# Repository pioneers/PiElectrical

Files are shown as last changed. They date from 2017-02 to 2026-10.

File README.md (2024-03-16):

# PiElectrical

This is the working repo for PiElectrical teams

1. [ToDo](#todo)
2. [Repo Structure](#repo-structure)
3. [Setup](#setup)
4. [Work Flow](#work-flow)
5. [How to Create a Gerber](#how-to-create-a-gerber)
6. [Docu Packets](#docu-packets)
7. [FAQ](#faq)
8. [Useful Links](#useful-links)
9. [Standards](#standards)

## ToDo:
* The stuff in PDB-Y16
* Convert motor controller design to KiCad
* Add and test current regulation for motor controller
* Talk to runtime and potentially use cheaper MCU for motor controller

[Back to Top](#pielectrical)

## Repo Structure:

**Boards**: Contains all necessary information about each board, including KiCad (and old Eagle) files, arduino test files, and board specific documentation.

**Bootloaders**: Contains the files necessary to burn the bootloader for boards identifying as Leonardo (Atmega32u4).

**Documentation**: All docu packets and scripts. *Fragile! Do not touch!*

**Production_Files**: Finalized gerbs and other necessary production files (BOM, CPL, etc...) sent out for fabrication.

**Images**: Place all your images in here to enhance your READMEs.

**Libraries**: Necessary KiCad files to work on PiElectrical

ToDo is on the README to keep things easier to see at first glance. GitHub issues tracker can be used as well.

[Back to Top](#pielectrical)

## Setup

<details>
    <summary>When you see an arrow like this... (click me)</summary>
        ...it indicates an expandable section. We usually include images in here as a better reference for you to follow along.
</details>

### Initial Setup of PiElectrical repo on your computer

1. Copy the URL for pioneers/PiElectrical to your clipboard: (Or here: https://github.com/pioneers/PiElectrical.git)
2. In Terminal (Mac, GNU/Linux) or Git Bash (windows), navigate to your working directory (the directory that you want to keep PiElectrical in.)
3. Clone PiElectrical by running this command: `git clone https://github.com/pioneers/PiElectrical.git`

### Installation of KiCad on your computer
1. Download the latest version of KiCad here: https://www.kicad.org/download/
2. <details>
    <summary>Run installer. Use all default settings on installer. (Click to see default settings)<br></summary>
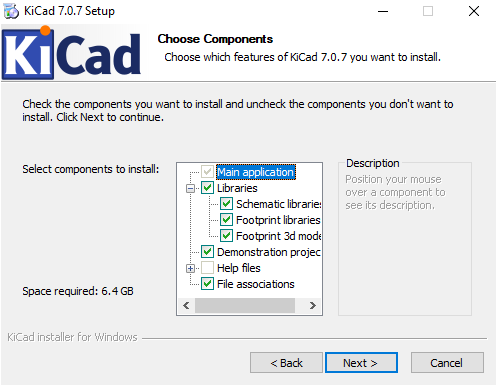
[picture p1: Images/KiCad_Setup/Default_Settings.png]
    
</details>

### Setting up KiCad
1. Open KiCad.
2. <details>
    <summary>Depending on whether you've used KiCad before, select the appropriate option on the pop-up. (Default settings if you're new to KiCad).</summary>
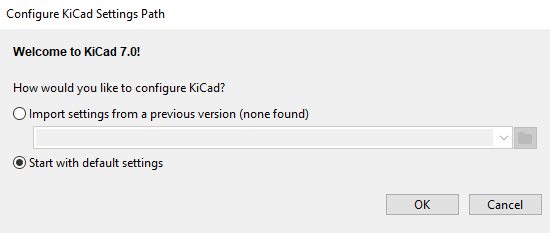
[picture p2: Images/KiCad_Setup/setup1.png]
    
   </details>

#### Adding Symbols
1. <details>
    <summary>Go to the <i>Preferences</i> tab, and select <i>Manage Symbol Libraries...</i></summary>
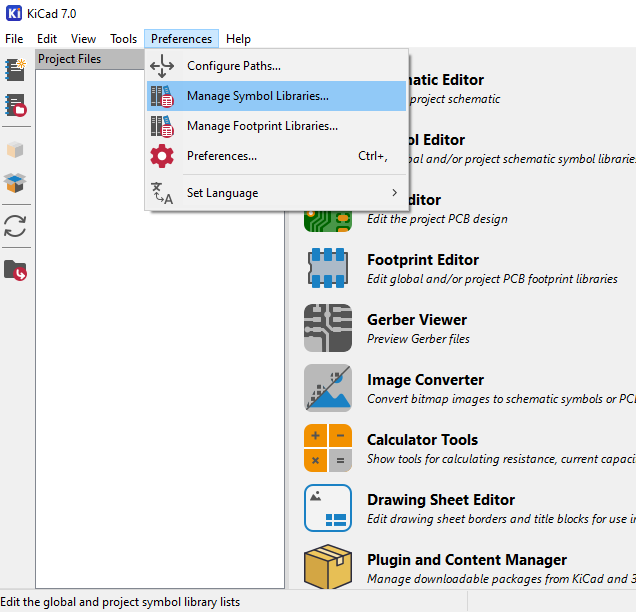
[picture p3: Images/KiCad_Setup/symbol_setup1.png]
    
   </details>
2. <details>
    <summary>If this is your first time using KiCad, it will prompt you to configure the <i>Global Symbol Library</i>. It is highly recommended that you select "Copy default global symbol library table".</summary>
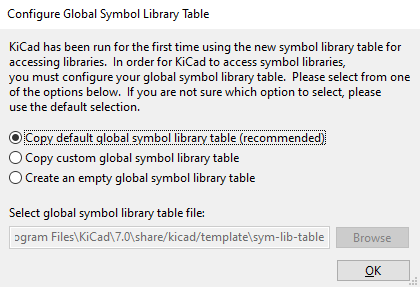
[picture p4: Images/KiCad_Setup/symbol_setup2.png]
    
   </details>
3. <details>
    <summary>Select the folder icon near the bottom left and navigate to the <i>PiE_Symbols.kicad_sym</i> file in the <i>src</i> folder.</summary>
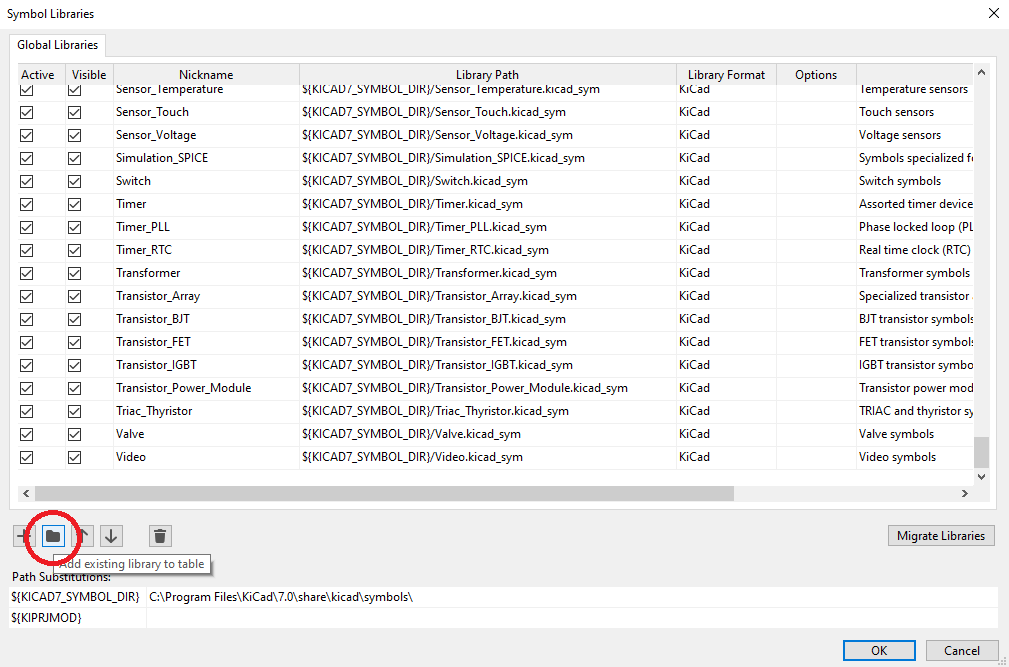
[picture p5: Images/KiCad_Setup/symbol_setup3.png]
    
   </details>
4. <details>
    <summary>You should now see the <i>PiE_Symbols</i> in your Symbol Libraries. Make sure the "active" box is checked, and click "OK".</summary>
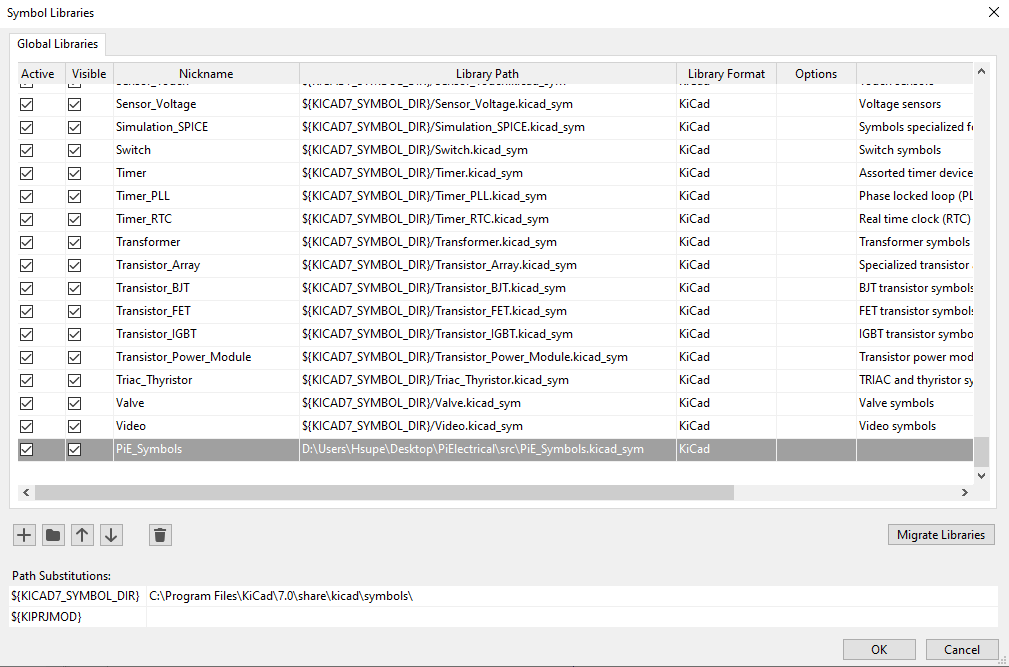
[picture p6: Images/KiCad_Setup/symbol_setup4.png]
    
   </details>

#### Adding Footprints
1. <details>
    <summary>Go to the <i>Preferences</i> tab, and select <i>Manage Footprint Libraries...</i></summary>
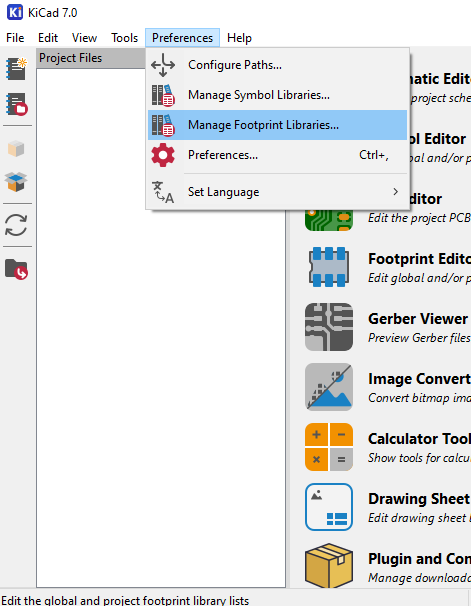
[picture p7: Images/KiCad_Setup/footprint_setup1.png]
    
   </details>
2. <details>
    <summary>If this is your first time using KiCad, it will prompt you to configure the <i>Global Footprint Library</i>. It is highly recommended that you select "Copy default global footprint library table".</summary>
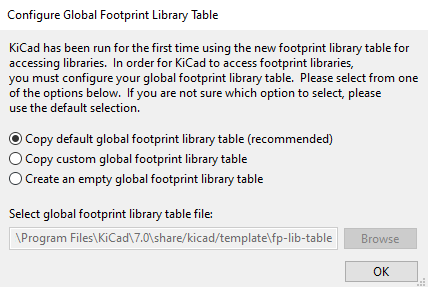
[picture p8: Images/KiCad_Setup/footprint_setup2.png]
    
   </details>
3. <details>
    <summary>Select the folder icon near the bottom left and navigate to the <i>PiE_Footprints.pretty</i> file in the <i>src</i> folder.</summary>
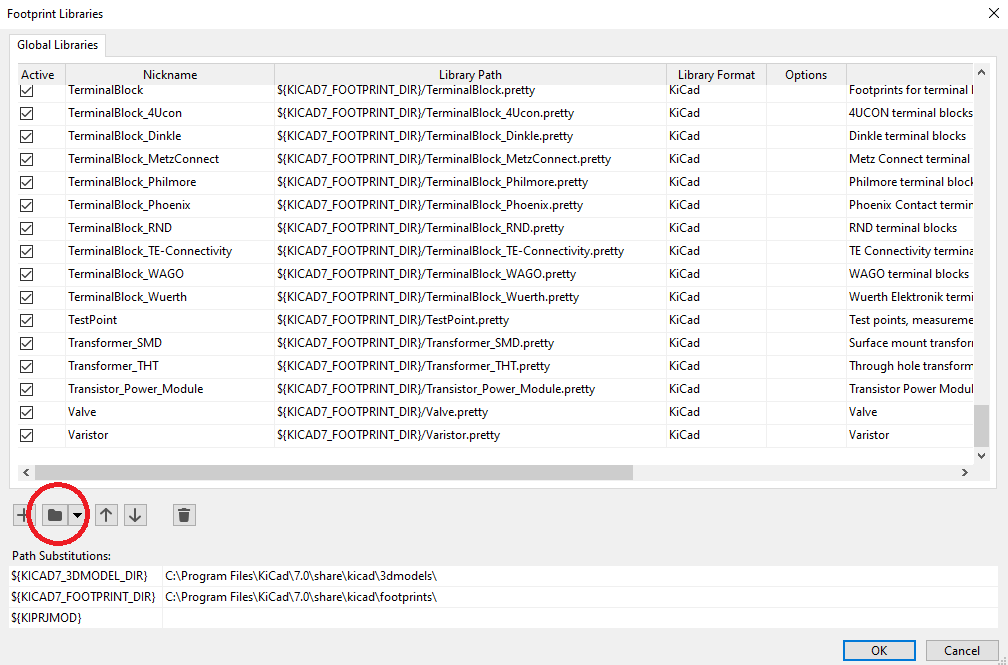
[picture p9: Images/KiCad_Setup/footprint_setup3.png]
    
   </details>
4. <details>
    <summary>You should now see the <i>PiE_Footprints</i> in your Footprint Libraries. Make sure the "active" box is checked, and click "OK".</summary>
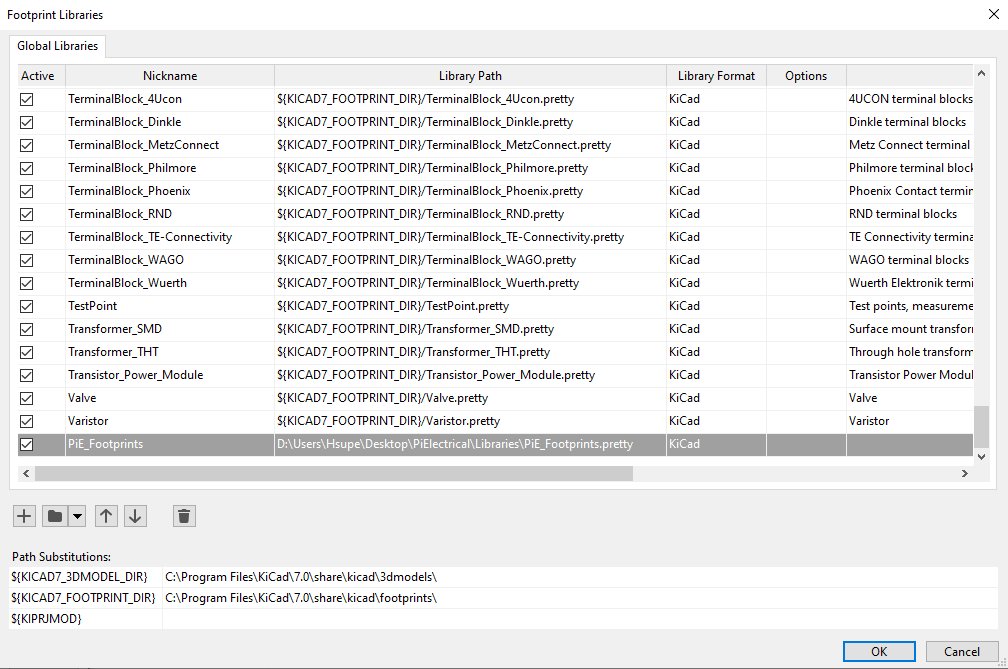
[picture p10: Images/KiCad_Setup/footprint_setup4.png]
    
   </details>

Note that this setup instruction is based on KiCad 7.0.7, but it should still work for other versions.

[Back to Top](#pielectrical)

## Work Flow

Protocol when working on KiCad files

The revision number should be *REV \<year\>\<revision\>*. E.g. **REV 16A** for year 16 revision A.

If you are not quite familiar with git, see [Useful Links](#useful-links) for the PiE Github tutorial

**WARNING**: Do not modify PiE_Symbols.kicad_sym or PiE_Footprints.pretty without discussing it with PMs.

### Steps when working on KiCad files:

1. In Terminal (mac, GNU/Linux) or GitBash (windows), navigate to your working directory (wherever you have PiElectrical).
2. Make sure your working directory is clean: git status
3. If you haven't started your sub project: git checkout -b YOURNAME-SUBPROJECT
  3. YOUR\_NAME/SUBPROJECT is now the name of your branch
4. Do your work in KiCad.
5. Once you are at a good stopping point in your KiCad work, commit your progress:
    1. git add path/to/your/file
    2. git commit -m "Make your commit message short and with this format"
    3. **NOTE**: Commiting is like saving your file, but for all of PiE as well as your personal computer. And just like saving, Commit Early & Commit Often!
6. Repeat Steps 5 and 6 until you are finished with your EAGLE work.
7. Once you have made your last commit, push your files to the PiElectrical github repo: git push origin YOUR\_BRANCH
    - If you get a merge conflict, contact the PMs for help.
8. If **completely** done, submit a Pull Request

### Commit Message Format Conventions

* Present Tense ("Reroute power traces on team flag", not "Rerouted power traces on team flag")
* No period at the end: ("Reroute power traces on team flag", not "Reroute power traces on team flag.")
* Keep your message length to about one sentence.

### Merge Conflicts: What should I do?

Don't try to fix it yourself: Eagle files are finicky and you might break all your work!

Ask someone who knows how to deal with this, i.e. your PM or something

[Back to Top](#pielectrical)

## Generating Fabrication Outputs

1. Make sure you run the Electrical Rules Check (ERC) in the schematic and the Design Rules Checker (DRC) in the layout, and have no *red* errors. Feel free to ask PMs if you have any questions.
2. <details>
    <summary>Go to File -> Fabrication Outputs -> Gerbers (.gbr)...</summary>
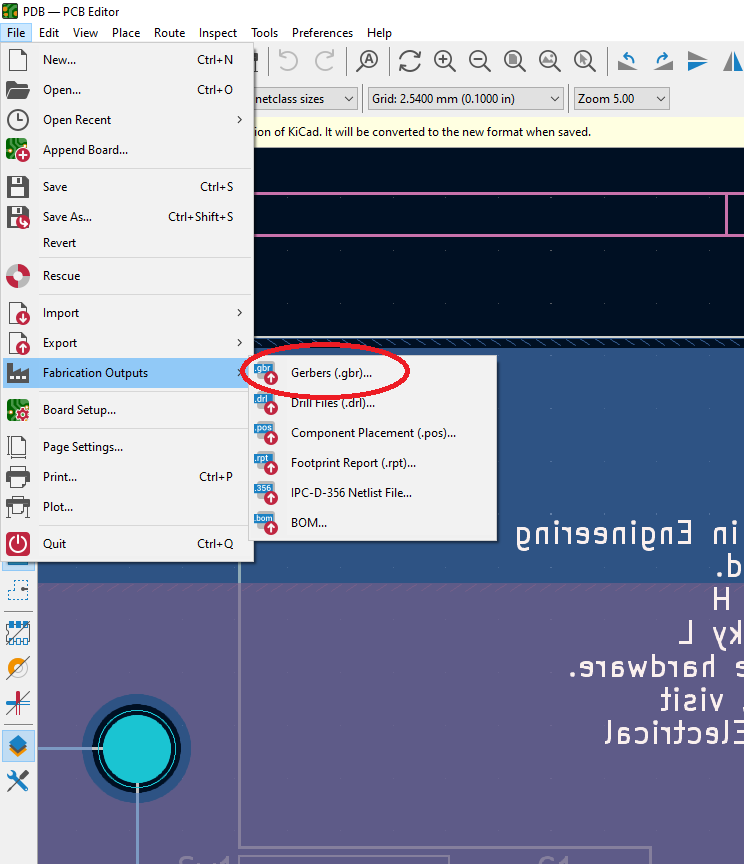
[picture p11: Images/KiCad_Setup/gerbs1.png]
    
   </details>
3. <details>
    <summary>If this is your first time using KiCad, it will prompt you to configure the <i>Global Symbol Library</i>. It is highly recommended that you select "Copy default global symbol library table".</summary>
    
   </details>
4. <details>
    <summary>Select the folder icon near the bottom left and navigate to the <i>PiE_Symbols.kicad_sym</i> file in the <i>src</i> folder.</summary>
    
   </details>
5. <details>
    <summary>You should now see the <i>PiE_Symbols</i> in your Symbol Libraries. Make sure the "active" box is checked, and click "OK".</summary>
    
   </details>

1. Open the brd file
2. Click Cam Job
3. Open pie.cam
4. Make a directory in each sensor's folder called SENSOR\_NAME-gerb
    * SENSOR\_NAME **must** be the exact name as the brd file
5. Run job, and click yes to all for the polygon issue
6. Once all the jobs are done, run `make gerb`

[Back to Top](#pielectrical)

## FAQ

Q: What's the difference between commit before I pull?

A: Do you want to keep any of the changes? Then commit those (the ones you want to keep) before you pull. Or else, the things you pull might conflict with your work, and you'll have a git disaster.

Q: I worked on my stuff, pulled, and everything I did went away!

A: As long as you committed, the PMs can recover your work for you.

Q: Why am I working on my own branch?

A: This is to keep track of pull request and board reviews on a per board basis

[Back to Top](#pielectrical)

## Useful Links

PiE's own [Github Tutorial](https://docs.google.com/a/pioneers.berkeley.edu/presentation/d/1ef5zSDMbE7dCu4XAC4dXhSV5iUd7gjCyXPjRrRvtbQI/edit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)

[PiElectrical Wiki](https://github.com/pioneers/PiElectrical/wiki)

[Markdown Cheatsheet](https://github.com/adam-p/markdown-here/wiki/Markdown-Cheatsheet)

[Arduino Pro Micro Pinouts](https://cdn.sparkfun.com/assets/9/c/3/c/4/523a1765757b7f5c6e8b4567.png)

[BAC DFM](http://instantdfm.bayareacircuits.com/)

Read up on the [PiE Electrical Style Rules and Guidelines](https://staff.pierobotics.org/wiki/Electrical_style_guidelines) (This is a good resource, but outdated)

[Back to Top](#pielectrical)

## Design Rules

You can find JLC's design rules here: https://jlcpcb.com/capabilities/pcb-capabilities. Please review this before ordering a PCB.

#### Some of our general rules:
- Traces **must** be multiples of 45 degrees
- Standard Pin Distance: 100 mils (2.54 mm)

#### Make sure to annotate your boards:

```
Copyright (c) 2023, Pioneers in Engineering
All rights reserved.

Design by: Justin H
This design is open source hardware.
For more information, visit 
github.com/pioneers/PiElectrical
```

[Back to Top](#pielectrical)

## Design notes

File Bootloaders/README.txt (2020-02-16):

avrdude toolchain setup (Windows 10):
	1) extract avrdude-win-64bit.zip to C:\Program Files.
	2) add C:\Program Files\avrdude to PATH
		- open Control Panel
		- go to System and Security 
		- choose System
		- on the left, choose Advanced system settings
		- select Environment Variables
		- on the top panel, select Path on the left and hit Edit...
		- choose Browse on the right and select the path, C:\Program Files\avrdude
		- hit ok
	
	3) install drivers for Pocket AVR Programmer: 
		- follow this tutorial: https://learn.sparkfun.com/tutorials/pocket-avr-programmer-hookup-guide/installing-drivers

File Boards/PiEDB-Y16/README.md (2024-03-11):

# Power Distribution Board
## Pioneers in Engineering Year 2023-2024
---
Continuation of Y15's PDB.
  
**To Do:**  
- Add battery calibration **(Added switch, WIP for runtime)**
- Create DC-DC Converter **(Work In Progress)**
- Fix battery shorting problem **(Complete)**
- Remove power from data port, optional power using shortings **(Complete)**
- Consider using different port for 5v **(Kept as USB)**

**To Do: Large Revision**
- Find a switch rated for 50A @ 12VDC
- Fuse each motor controller port with 7.5A slow-blow fuse (MC rated for 2x 3.5A motors) (Blows in 20Sec at 10A)
- Add 40A slow-blow fuse for battery. (Blows in 5 min @ 50A, Blows in 20 sec @ 55A) (Battery Max is 55A)
- Add 7.5A slow-blow fuse for 5V rail. (Follows 7.5A max in dc-dc converter)
- Add additional USB plug    
- Rework traces/power planes for large current

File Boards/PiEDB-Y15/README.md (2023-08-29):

# Power Distribution Board
## Pioneers in Engineering Year 2022-2023
---
We are basing our design on the Y9 PDB design. We will use a toggle switch instead of the circuit breaker to power on the device, and a fuse in series with the battery as a safety feature. This is an effort to cut costs.  
  
**Features:**  
- Anderson Connectors (A{1-5}) provide 12v power to motor controllers and other components that require 12v.
- USB-A Ports (USB{1-3}) provide 5v power to Le Potato computer and other components that require 5v.
- USB-A Port (DATA1) sends serial data from the PDB to the Le Potato computer.
- Rocker Switch (Sw1) turns on the board, thereby turning on the robot.
- SPST Switch (Sw2) selects which network the robot should be connected to.
- Disable Buzzing Pins (J1) disables buzzing from low battery when shorted.

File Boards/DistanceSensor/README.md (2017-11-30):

# **DISTANCESENSOR**

[Distance Sensor](https://www.aliexpress.com/item/Free-shipping-1pcs-Ultrasonic-Module-HC-SR04-Distance-Measuring-Transducer-Sensor-for-Arduino-Samples-Best-prices/32640823431.html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)

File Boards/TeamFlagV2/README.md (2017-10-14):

# TeamFlag

* ~~make the holes where the USB goes in SMALLER~~
* ~~add "+" and "-" to those holes so u know what they r~~

REV B CHANGES NEEDED
* find a USB that we don't have to strip and is shorter

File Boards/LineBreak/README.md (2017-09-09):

# Line Break

Yellow wire: digital read. 1 if connection maintained between emitter and receiver. 0 if broken.

5v powered

15cm range

[Datasheet](https://cdn-shop.adafruit.com/product-files/2167/C2916.pdf)

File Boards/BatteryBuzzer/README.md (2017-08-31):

#Battery Buzzer

Reacts the how angry the battery is.  This design is an experimental board using the magic TI chip.

[Really good pro micro reference](https://cdn.sparkfun.com/assets/9/c/3/c/4/523a1765757b7f5c6e8b4567.png)

[Proposed multiplexer (analog)](http://www.ti.com/product/sn74hc4852/)
* $0.72 ea
* Dual 4:1 multiplexer
* Multiple package types
* Supports up to 6v VCC 

[Backup multiplexer](http://www.ti.com/product/SN74CB3T3253/)
* Use in case the other one doesn't work

[OP-AMP (Through-Hole)](http://www.ti.com/product/TL072/description)
* Cheaper - $0.69 ea

[ADC](http://www.ti.com/product/ADS1100/description)

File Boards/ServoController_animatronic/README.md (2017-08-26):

#Servo Controller

Previous Named Koala Bear, controls the servo

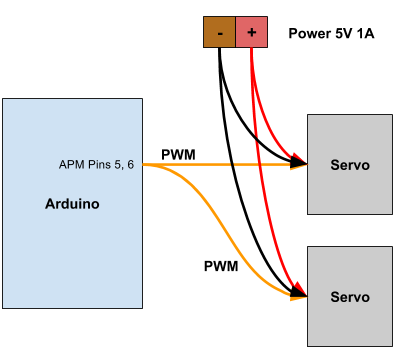
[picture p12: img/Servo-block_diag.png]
Block Diagram


Has 2 Servo Mounts, external 5 V and Max 1 Amp

Y9: We reduced the number of servos per board, no one complained, so we'll keep it this way to maintain a small formfactor. Think more about enclosure! It was the most stable board.

Y10: Avererorerol Kandala

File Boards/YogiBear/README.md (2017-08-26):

#YOGI BEAR

Yogi Bear is a cool bear.

[VNH2SP30](https://www.aliexpress.com/item/Free-shipping-VNH2SP30-in-stock/32235666194.html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,searchweb201602_4_10056_10065_10055_10068_10067_10054_10069_10059_418_10073_10017_10070_10060_10061_10052_10062_10053_10050_10051,searchweb201603_3&btsid=7e6b3cdb-1352-4e9c-9080-e427ead57444)

[MOSFET DIGI REEL] (http://www.digikey.com/product-detail/en/infineon-technologies/IPD90N03S4L-02/IPD90N03S4L-02DKR-ND/2231371)

[MOSFET CUT TAPE] (http://www.digikey.com/product-detail/en/infineon-technologies/IPD90N03S4L-02/IPD90N03S4L-02CT-ND/2231143)

Y9: Wasn't used because we used twist-it as the interface to the red boards.  We probably should continue doing it this way.

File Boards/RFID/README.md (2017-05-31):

# RFID

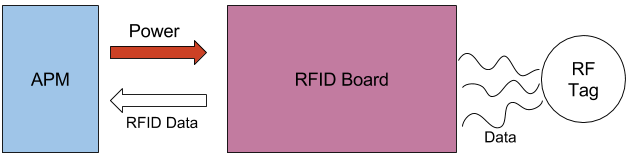
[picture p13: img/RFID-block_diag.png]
Block Diagram


Identifies [RFID chips](https://www.aliexpress.com/item/High-Quality-MFRC-522-RC522-RFID-Reader-RF-IC-Card-Inductive-Sensor-Module-For-Arduino-Module/32657638702.html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)

[Documentation](https://github.com/miguelbalboa/rfid)

Pinouts:

RFID | Arduino Pro Micro
---- | -----------------
RST | 9
SDA | 10
MOSI | 16
MISO | 14
SCK | 15
3.3V | VCC
GND | GND

**Y9**: They worked fine, very stable and got a good yield rate. The enclosure could have been just a TAD bigger to accomodate for the USB connection.

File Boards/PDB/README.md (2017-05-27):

# PiEDB

Y9: Things went for a huge spin. We produced our own PDB for the first time integrated with a battery buzzer that we designed in house. It had a 7 segment display and was able to be calibrated. The PDB itself still used near useless fuses. The 12V line used Andersons for the motors and the 5V line used ATX connetors for the first time. This made things much easier for the students. The circuit breaker is still quite an expensive on/off switch, so it can be replaced with something else perhaps. SMAKM 5V regulator is also quite expensive. There was also discussion on how the 5V rail would not be steady enough to power multiple devices, e.x. teams had USB hubs that would disconnect upon impact.

Y10: Nicholas Werbliblub

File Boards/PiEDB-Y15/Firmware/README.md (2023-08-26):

# Power Distribution Board
## Firmware - Some basic code to see if the hardware works.
---
For the working code, please refer to Runtime. \
https://github.com/pioneers/runtime
  
**To Do:**  
- change this readme to be more descriptive

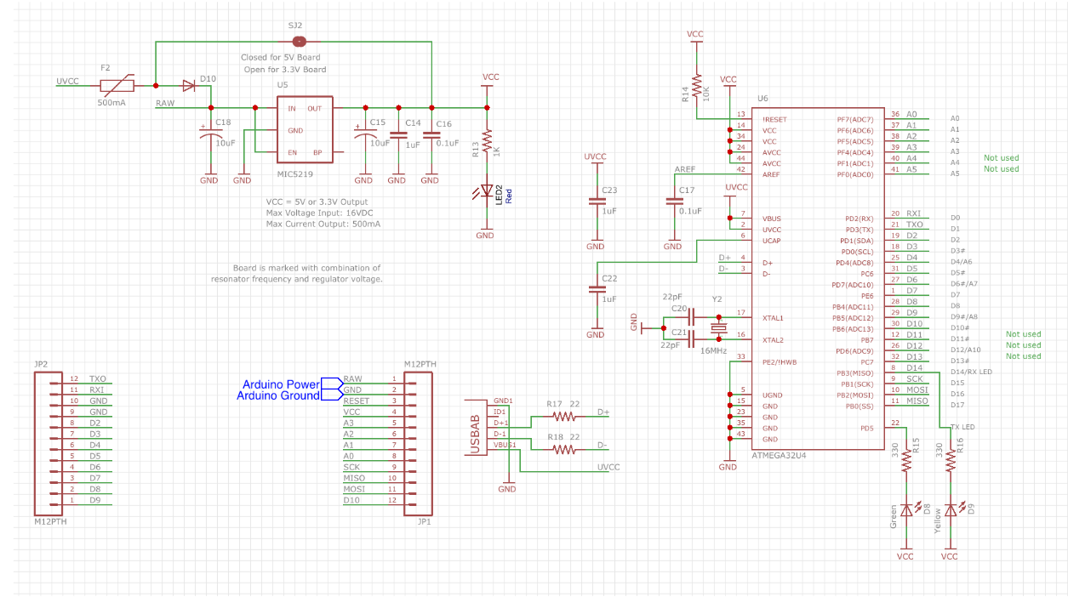
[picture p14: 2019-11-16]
Boards/PDB2/PDB Firmware Files/pro micro schematic.PNG

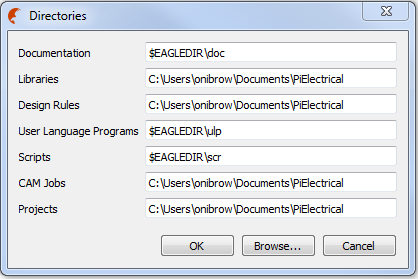
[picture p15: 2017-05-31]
Images/eagle-directories.PNG

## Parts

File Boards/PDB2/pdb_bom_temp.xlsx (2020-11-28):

Qty | Value | Device | Package | Parts | Description | DATASHEETURL | DCR | DESCRIPTION | DISTRIBUTOR | DISTRIBUTOR_PART_NUMBER | IDC | L | MANUFACTURER | MANUFACTURER_NAME | MANUFACTURER_PART_NO | MANUFACTURER_PART_NUMBER | NOTES | PACKAGE | PACKAGE_DESIGNATOR | PARTNUMBER | PART_NO | PIE-DIGIKEY-PN-ALT1 | PIE-DIGIKEY-PN-PRI | PIE-INT-REF-NUM | PROD_ID | REFDES | SF_ID | TYPE | VALUE | VENDOR
1 |  | BUZZER3.3VBUZZER | BUZZER_3.3V | BUZ1 | Buzzer
1 |  | CRYSTAL10.5X4.8 | CRYSTAL-SMD-10.5X4.8-2PIN | Y1 | Various standard crystals. Proven footprints. Spark Fun Electronics SKU : COM-00534 |  |  |  |  |  |  |  |  |  |  |  |  |  |  |  | ECS-160-20-3X-EN-TR |  |  | CRYSTAL
1 |  | JMP-OPTION | 1X03-JMP-OPTION | JP7 | A 3 pin header with silk screen indicating jumper positions to select an option.
5 |  | LED0805 | LED-0805 | LED1, LED2, LED3, LED4, LED5 | LEDs |  |  |  |  |  |  |  |  |  |  |  |  |  |  |  |  |  |  | LED
1 |  | M041X04-MTA | 1X04-MTA | JP1 | 4-pin 0.1-inch header and MTA connector |  |  |  |  |  |  |  |  |  |  |  |  |  |  |  |  |  |  | MTA
2 | .1uF | CAP0603-CAP | 0603-CAP | C4, C8 | Capacitor |  |  |  |  |  |  |  |  |  |  |  |  |  |  |  |  |  |  | CAPACITOR-GENERIC
1 | 100k | R-US_R0603 | R0603 | R6 | RESISTOR, American symbol |  |  | RESISTOR, American symbol | DigiKey |  |  |  | Rohm Semiconductor |  |  |  | Cut Tape | R0603 |  |  |  |  |  |  |  |  |  |  | >VALUE
5 | 10k | R-US_R0603 | R0603 | R1, R2, R8, R11, R12 | RESISTOR, American symbol |  |  | RESISTOR, American symbol | DigiKey |  |  |  | Rohm Semiconductor |  |  |  | Cut Tape | R0603 |  |  |  |  |  |  |  |  |  |  | >VALUE
2 | 10uF | CAP0805 | 805 | C5, C6 | Capacitor |  |  |  |  |  |  |  |  |  |  |  |  |  |  |  |  |  |  | CAPACITOR-GENERIC
2 | 10uF | CAP_POLRADIAL | .248CAP_THRU" | C11, C14 | Capacitor Polarized
10 | 150R | R-US_R0603 | R0603 | R18, R19, R20, R21, R22, R23, R24, R25, R26, R27 | RESISTOR, American symbol |  |  | RESISTOR, American symbol | DigiKey |  |  |  | Rohm Semiconductor |  |  |  | Cut Tape | R0603 |  |  |  |  |  |  |  |  |  |  | >VALUE
2 | 18pF | CAP0603-CAP | 0603-CAP | C12, C13 | Capacitor |  |  |  |  |  |  |  |  |  |  |  |  |  |  |  |  |  |  | CAPACITOR-GENERIC
4 | 1uF | CAP0603-CAP | 0603-CAP | C2, C10, C15, C16 | Capacitor |  |  |  |  |  |  |  |  |  |  |  |  |  |  |  |  |  |  | CAPACITOR-GENERIC
3 | 2.2uF | CAP0603-CAP | 0603-CAP | C1, C3, C17 | Capacitor |  |  |  |  |  |  |  |  |  |  |  |  |  |  |  |  |  |  | CAPACITOR-GENERIC
5 | 220R | R-US_R0603 | R0603 | R13, R14, R15, R16, R17 | RESISTOR, American symbol |  |  | RESISTOR, American symbol | DigiKey |  |  |  | Rohm Semiconductor |  |  |  | Cut Tape | R0603 |  |  |  |  |  |  |  |  |  |  | >VALUE
2 | 22R | R-US_R0603 | R0603 | R28, R29 | RESISTOR, American symbol |  |  | RESISTOR, American symbol | DigiKey |  |  |  | Rohm Semiconductor |  |  |  | Cut Tape | R0603 |  |  |  |  |  |  |  |  |  |  | >VALUE
2 | 3.3k | R-US_R0603 | R0603 | R3, R4 | RESISTOR, American symbol |  |  | RESISTOR, American symbol | DigiKey |  |  |  | Rohm Semiconductor |  |  |  | Cut Tape | R0603 |  |  |  |  |  |  |  |  |  |  | >VALUE
1 | 3.3uH | L_VLP8040T-3R3N | VLP8040 | L1 |  | httpwww.tdk.co.jptjfx01j531_vlp.pdf | 0.02 | Unknown |  |  | 5.2 | 3300000 | TDK | TDK |  | VLP8040T3R3N |  |  | VLP8040 |  |  |  |  |  |  |  |  |  |  | TDK
1 | 47uF | CAP0805 | 805 | C9 | Capacitor |  |  |  |  |  |  |  |  |  |  |  |  |  |  |  |  |  |  | CAPACITOR-GENERIC
1 | 499k | R-US_R0603 | R0603 | R5 | RESISTOR, American symbol |  |  | RESISTOR, American symbol | DigiKey |  |  |  | Rohm Semiconductor |  |  |  | Cut Tape | R0603 |  |  |  |  |  |  |  |  |  |  | >VALUE
1 | 56.2k | R-US_R0603 | R0603 | R10 | RESISTOR, American symbol |  |  | RESISTOR, American symbol | DigiKey |  |  |  | Rohm Semiconductor |  |  |  | Cut Tape | R0603 |  |  |  |  |  |  |  |  |  |  | >VALUE
1 | 5m | SHUNT_SMD | SMD_SHUNT | R7 |  |  |  |  |  |  |  |  |  |  | WSHM28185L000FEA
1 | 8.2nF | CAP0603-CAP | 0603-CAP | C7 | Capacitor |  |  |  |  |  |  |  |  |  |  |  |  |  |  |  |  |  |  | CAPACITOR-GENERIC
3 | ANDERSONVERTICAL | ANDERSONVERTICAL | ANDERSON_VERTICAL | CONN1, CONN2, CONN3 | 2-pin 25A Anderson Connector |  |  |  |  |  |  |  |  |  |  |  |  |  |  |  |  |  |  | Anderson
1 | ATMEGA32U4-AU | ATMEGA32U4-AU | TQFP44 | U3 |  |  |  |  |  |  |  |  |  |  |  |  |  |  |  |  |  | ATMEGA32U4-MURCT-ND | ATMEGA32U4RC-MURCT-ND | ATmega32U4
4 | ATX | ATX | ATX | JP2, JP3, JP4, JP5 | ATX 2 Pin Connector
1 | AVR_SPI_PRG_6MA03-2 | AVR_SPI_PRG_6MA03-2 | MA03-2 | J2 | AVR ISP 6 Pin |  |  |  |  |  |  |  |  |  |  |  |  |  |  |  |  |  |  | BULK-STOCK
1 | BAR_SEGMENT_DISPLAY | BAR_SEGMENT_DISPLAY | BAR_SEGMENT_DISPLAY | LED6
1 | BQ7692006PWRPW20-M | BQ7692006PWRPW20-M | PW20-M | U1 |  |  |  |  |  |  |  |  |  |  |  | BQ7692006PWR |  |  |  |  |  |  |  |  |  |  |  |  |  | Texas Instruments
1 | D_MBR1020VL | D_MBR1020VL | SOD-123FL | D2 |  |  |  |  |  |  |  |  |  |  |  |  |  |  |  |  | MBR1020VL
1 | NMOS_CSD17579Q3A | NMOS_CSD17579Q3A | DNH0008A | M1 |  |  |  |  |  |  |  |  |  |  |  | CSD16401Q5 |  |  |  |  |  |  |  |  |  |  |  |  |  | Texas Instruments
1 | PUSH_BUTTON | PUSH_BUTTON | BUTTON_K12A | SW1
6 | STAND-OFFTIGHT | STAND-OFFTIGHT | STAND-OFF-TIGHT | STANDOFF1, STANDOFF2, STANDOFF3, STANDOFF4, STANDOFF5, STANDOFF7 | #4 Stand Off |  |  |  |  |  |  |  |  |  |  |  |  |  |  |  |  |  |  | DNL
1 | USB_B_PTH | USB_B_PTH | USB-B-PTH | J3 | USB Type B Connector |  |  |  |  |  |  |  |  |  |  |  |  |  |  |  |  |  |  |  | CONN-08278 |  | PRT-00139
1 | Value | TPS563210ADDFR | DDF0008A_N | U2 |  |  |  |  |  |  |  |  | Texas Instruments | Texas Instruments |  | TPS563210ADDFR |  |  |  | TPS563210ADDFR |  |  |  |  |  | RefDes |  | TYPE | Value
1 | XT60CONNECTOR | XT60CONNECTOR | XT60CONNECTOR | J1 | 12V XT60 power connector |  |  |  |  |  |  |  |  |  |  |  |  |  |  | PRT-10474

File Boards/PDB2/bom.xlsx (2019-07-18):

Qty | Value | Device | Package | Parts | Description | DESCRIPTION | DISTRIBUTOR | DISTRIBUTOR_PART_NUMBER | MANUFACTURER | MANUFACTURER_NAME | MANUFACTURER_PART_NO | MANUFACTURER_PART_NUMBER | NOTES | PACKAGE | PARTNUMBER | PIE-INT-REF-NUM | PROD_ID | REFDES | SF_ID | TYPE | VALUE | VENDOR
1 |  | ATMEGA328PB-AU | TQFP32-08 | U3
1 |  | CONN_02 | 1X02 | J12 | Multi connection point. Often used as Generic Header-pin footprint for 0.1 inch spaced/style header connections
1 |  | CONN_05X2NO_SILK | 2X5_NOSILK | J11 | Multi connection point. Often used as Generic Header-pin footprint for 0.1 inch spaced/style header connections
1 |  | ECX-53BSMDCRYSTAL | SMD_CRYSTAL | Y1 |  |  |  |  |  |  | ECS-80-18-30B-AGN-TR
1 |  | M03PTH | 1X03 | J9 | 3-pin 0.1-inch header and MTA connector |  |  |  |  |  |  |  |  |  |  | BULK-STOCK
1 |  | M041X04-MTA | 1X04-MTA | J2 | 4-pin 0.1-inch header and MTA connector |  |  |  |  |  |  |  |  |  |  | MTA
2 | .1uF | CAP0603-CAP | 0603-CAP | C4, C6 | Capacitor |  |  |  |  |  |  |  |  |  |  | CAPACITOR-GENERIC
1 | 1000pF | CAP0603-CAP | 0603-CAP | C7 | Capacitor |  |  |  |  |  |  |  |  |  |  | CAPACITOR-GENERIC
1 | 100k | R-US_R0603 | R0603 | R20 | RESISTOR, American symbol | RESISTOR, American symbol | DigiKey |  | Rohm Semiconductor |  |  |  | Cut Tape | R0603 |  |  |  |  |  |  | >VALUE
3 | 10k | R-US_R0603 | R0603 | R3, R5, R9 | RESISTOR, American symbol | RESISTOR, American symbol | DigiKey |  | Rohm Semiconductor |  |  |  | Cut Tape | R0603 |  |  |  |  |  |  | >VALUE
1 | 10uF | CAP0603-CAP | 0805-CAP | C5 | Capacitor |  |  |  |  |  |  |  |  |  |  | CAPACITOR-GENERIC
2 | 18pF | CAP0603-CAP | 0603-CAP | C9, C10 | Capacitor |  |  |  |  |  |  |  |  |  |  | CAPACITOR-GENERIC
2 | 1uF | CAP0603-CAP | 0603-CAP | C2, C11 | Capacitor |  |  |  |  |  |  |  |  |  |  | CAPACITOR-GENERIC
2 | 2.2uF | CAP0603-CAP | 0603-CAP | C1, C3 | Capacitor |  |  |  |  |  |  |  |  |  |  | CAPACITOR-GENERIC
1 | 2.2uH | ASPI-0530_INDUCTOR | ASPI | L1
10 | 220 | R-US_R0603 | R0603 | R10, R11, R12, R13, R14, R15, R16, R17, R18, R19 | RESISTOR, American symbol | RESISTOR, American symbol | DigiKey |  | Rohm Semiconductor |  |  |  | Cut Tape | R0603 |  |  |  |  |  |  | >VALUE
1 | 220mV | DIODESOD-323 | SOD-323 | D1 | Diode |  |  |  |  |  |  |  |  |  |  | DIODE
1 | 22uF | CAP0603-CAP | 0805-CAP | C8 | Capacitor |  |  |  |  |  |  |  |  |  |  | CAPACITOR-GENERIC
2 | 3.3k | R-US_R0603 | R0603 | R1, R2 | RESISTOR, American symbol | RESISTOR, American symbol | DigiKey |  | Rohm Semiconductor |  |  |  | Cut Tape | R0603 |  |  |  |  |  |  | >VALUE
1 | 499k | R-US_R0603 | R0603 | R7 | RESISTOR, American symbol | RESISTOR, American symbol | DigiKey |  | Rohm Semiconductor |  |  |  | Cut Tape | R0603 |  |  |  |  |  |  | >VALUE
1 | 5.6k | R-US_R0603 | R0603 | R6 | RESISTOR, American symbol | RESISTOR, American symbol | DigiKey |  | Rohm Semiconductor |  |  |  | Cut Tape | R0603 |  |  |  |  |  |  | >VALUE
1 | 5m | R-US_R2512 | R2512 | R8 | RESISTOR, American symbol |  |  |  |  |  | WSHM28185L000FEA‎ |  |  |  |  | RESISTOR-GENERIC
2 | ANDERSONVERTICAL | ANDERSONVERTICAL | ANDERSON_VERTICAL | J3, J4 | 2-pin 25A Anderson Connector |  |  |  |  |  |  |  |  |  |  | Anderson
4 | ATX | ATX | ATX | J5, J6, J7, J8 | ATX 2 Pin Connector
1 | AVR_SPI_PROG_5X2LOCK | AVR_SPI_PROG_5X2LOCK | 2X5-SHROUDED_LOCK | J10 | AVR 10-pin ICSP Header |  |  |  |  |  |  |  |  |  |  |  | CONN-08671 |  | PRT-08506
1 | BAR_SEGMENT_DISPLAY | BAR_SEGMENT_DISPLAY | BAR_SEGMENT_DISPLAY | LED1
1 | BQ7692006PWRPW20-M | BQ7692006PWRPW20-M | PW20-M | U1 |  |  |  |  |  |  |  | BQ7692006PWR |  |  |  |  |  |  |  |  |  | Texas Instruments
1 | D6C90F1LFS | D6C90F1LFS | D6C_BUTTON | BUT1
2 | STD20NF06LDPAK-M | STD20NF06LDPAK-M | DPAK-M | M1, M2 |  |  |  |  |  |  |  | STD20NF06L |  |  |  |  |  |  |  |  |  | STMicroelectronics
1 | Value | TPS62133RGTR | RGT0016C | U2 |  |  |  |  | Texas Instruments | Texas Instruments |  | TPS62133RGTR |  |  | TPS62133RGTR |  |  | RefDes |  | TYPE | Value
1 | XT60CONNECTOR | XT60CONNECTOR | XT60CONNECTOR | J1 | 12V XT60 power connector |  |  |  |  |  |  |  |  |  | PRT-10474

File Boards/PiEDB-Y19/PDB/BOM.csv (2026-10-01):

Id | Designator | Footprint | Quantity | Designation | Supplier and ref
1 | 5V1, GND1, MCU_5V1, USB_VBUS1 | TestPoint_Loop_D2.60mm_Drill0.9mm_Beaded | 4 | TestPoint
2 | A1, A2, A3, A4, A5 | anderson_horizontal | 5 | Anderson_Horizontal
3 | B1 | Buzzer | 1 | Buzzer
4 | Batt1 | AMASS_XT60-M_1x02_P7.20mm_Vertical | 1 | XT60_F
5 | C1, C2 | CP_Radial_D5.0mm_P2.00mm | 2 | 10u
6 | C8, C9, C10, C11, C16 | C_0603_1608Metric | 5 | 100nF
7 | C12, C15, C17, C18, C19 | C_0603_1608Metric | 5 | 1uF
8 | C13, C14 | C_0603_1608Metric | 2 | 18pF
9 | Converter1 | 5v_converter | 1 | 5v_converter
10 | D3 | LED-SEG-TH_12P-L30.0-W13.7-P2.54-S10.16-BL | 1 | 4_digit_7_segment_display
11 | D4, D7, D8, D9 | LED_0805_2012Metric | 4 | RED
12 | D5 | LED_0805_2012Metric | 1 | YELLOW
13 | D6 | LED_0805_2012Metric | 1 | GREEN
14 | F1 | Fuse Holder SMD | 1 | Fuseholder
15 | J1 | PinHeader_1x02_P2.54mm_Vertical | 1 | Conn_01x02
16 | J2 | PinHeader_1x04_P2.54mm_Vertical | 1 | Conn_01x04
17 | J3 | USB_B_OST_USB-B1HSxx_Horizontal | 1 | USB_B
18 | J4 | PinHeader_2x03_P2.54mm_Vertical | 1 | AVR-ISP-6
19 | Jst1 | JST_XH_B4B-XH-A_1x04_P2.50mm_Vertical | 1 | JST-XH_4-pin
20 | Q1 | s8050 JSMSEMI | 1 | s8050_JSMSEMI
21 | Q2, Q3, Q4 | SOT-23 | 3 | BSS84
22 | Q5, Q6, Q7 | SOT-23 | 3 | 2N7002
23 | Q8, Q9, Q10, Q11 | SOT-23 | 4 | MMBT3906
24 | R1, R3, R5 | R_0603_1608Metric | 3 | 30000
25 | R2, R4, R6 | R_0603_1608Metric | 3 | 10000
26 | R7, R8, R9, R10, R11, R12, R13, R14 | R_0603_1608Metric | 8 | 200
27 | R15 | R_0603_1608Metric | 1 | 3300
28 | R16 | R_0603_1608Metric | 1 | 1000
29 | R17, R18 | R_0603_1608Metric | 2 | 22
30 | R21, R36, R37, R38, R39 | R_0402_1005Metric | 5 | 10k
31 | R22, R23, R24 | R_0603_1608Metric | 3 | 100k
32 | R25 | R_0603_1608Metric | 1 | 10k
33 | R26, R27, R28, R29, R30, R31 | R_0603_1608Metric | 6 | 330
34 | R32, R33, R34, R35 | R_0603_1608Metric | 4 | 1k
35 | REF**, REF**, REF**, REF** | Hole_R1.62mm | 4 | Hole_R1.62mm
36 | Sw1 | Rocker Switch | 1 | D-SWITCH_MR5-111-C5N-BB
37 | SW2 | DEALON SS-12D01-G3 | 1 | SW_SPDT
38 | SW3 | SW_PUSH_6mm | 1 | SW_MEC_5E
39 | SW4 | SW_PUSH_6mm | 1 | RESET
40 | U4 | QFN-44-1EP_7x7mm_P0.5mm_EP5.2x5.2mm | 1 | ATmega32U4-M
41 | U5, U6 | SOT-363_SC-70-6 | 2 | LM66100DCK
42 | U7 | SOT-23-6 | 1 | USBLC6-2SC6
43 | USB1, USB2, USB3 | USB-A_female | 3 | USB
44 | Y2 | Crystal_SMD_5032-2Pin_5.0x3.2mm | 1 | 16MHz

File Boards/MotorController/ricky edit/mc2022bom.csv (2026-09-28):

Comment | Designator | Footprint | JLCPCB Part #
330 Ω Res Array | R4 | 0603_x4 | C29718
10 kΩ Res Array | R5 | 0603_x4 | C12018
0.1 µF | C9, C10, C11, C12 | 0402-CAP | C1525
1 uF | C7, C8 | 0603-CAP | C15849
16 MHz Crystal | Y1 | SMD-5032_2P | C112572
0.1 µF | C1, C3 | 0603-CAP | C14663
10 kΩ | R1, R2, R3 | R0603 | C25804
18 pF | C5, C6 | 0603-CAP | C1647
22 Ω | R6, R7 | R0603 | C23345
Atmega 32U4 | U1 | QFN-44_7x7x05P | C45874
330 Ω | R8 | R0603 | C23138
47 µF | C2, C4 | 1206 | C96123
DRV8872DDAR Motor Driver | MC1, MC2 | HSOP-8 | C114179
Green LED | LED3 | LED-0805 | C63855
100 µF Electrolytic | C13, C14 | SMD,6.3x5.3mm | C134723
Red LED | LED1, LED4, LED5 | LED-0805 | C72037
Yellow LED | LED2 | LED-0805 | C72036

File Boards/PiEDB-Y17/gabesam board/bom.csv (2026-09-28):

Reference | Value | Datasheet | Footprint | Qty | DNP
C1 | 3300 p | ~ | Capacitor_SMD:C_1206_3216Metric | 1
C2 | 0.1 u | ~ | Capacitor_SMD:C_1206_3216Metric | 1
C_ADJ1 | 1000 p | ~ | Capacitor_SMD:C_1206_3216Metric | 1
C_BYP1 | 1 u | ~ | Capacitor_SMD:C_1206_3216Metric | 1
C_IN1 | 33 u | ~ | Capacitor_SMD:C_1206_3216Metric | 1
C_OUT1 | 100 u | ~ | Capacitor_SMD:C_1206_3216Metric | 1
C_VCC1 | 0.47 u | ~ | Capacitor_SMD:C_1206_3216Metric | 1
D1 | D_Schottky_Filled | ~ | Diode_SMD:D_1206_3216Metric_Pad1.42x1.75mm_HandSolder | 1
GND1,GND2,SHUTDOWN1,V_SW1 | TestPoint | ~ | TestPoint:TestPoint_Loop_D2.60mm_Drill0.9mm_Beaded | 4
L1 | 15 u | ~ | Inductor_SMD:L_1206_3216Metric | 1
Q1 | PMOS | https://ngspice.sourceforge.io/docs/ngspice-html-manual/manual.xhtml#cha_MOSFETs | Package_SO:PowerPAK_SO-8_Single | 1
R1 | 1 m | ~ | Resistor_SMD:R_1206_3216Metric | 1
R_3 | 66.5 k | ~ | Resistor_SMD:R_1206_3216Metric | 1
R_ADJ1 | 2.1 k | ~ | Resistor_SMD:R_1206_3216Metric | 1
R_FB1 | 3.4 k | ~ | Resistor_SMD:R_1206_3216Metric | 1
R_FB2 | 10 k | ~ | Resistor_SMD:R_1206_3216Metric | 1
R_SEN1 | 0.01 | ~ | Resistor_SMD:R_1206_3216Metric | 1
R_T1 | 90.9 k | ~ | Resistor_SMD:R_1206_3216Metric | 1
U1 | ~ |  | PiE_Footprints:LM25085-Q1 | 1
V_IN1,V_Testpoint1 | 7 V to 42 V | ~ | TestPoint:TestPoint_Loop_D2.60mm_Drill0.9mm_Beaded | 2
V_OUT1 | 5 V | ~ | TestPoint:TestPoint_Loop_D2.60mm_Drill0.9mm_Beaded | 1

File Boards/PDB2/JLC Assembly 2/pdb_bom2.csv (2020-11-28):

Comment | Designator | Footprint | LCSC Part #
Red LED | LED1 | LED_0805 | C84256
Red LED | LED2 | LED_0806 | C84256
Red LED | LED3 | LED_0807 | C84256
Red LED | LED4 | LED_0808 | C84256
Red LED | LED5 | LED_0809 | C84256
TPS563200DDCR | U2 | SOT-23-6L | C97253
.1uF Cap | C4 | 603 | C14663
.1uF Cap | C8 | 603 | C14663
100k Res | R6 | 603 | C25803
10k Res | R1 | 603 | C25804
10k Res | R2 | 603 | C25804
10k Res | R8 | 603 | C25804
10k Res | R11 | 603 | C25804
10k Res | R12 | 603 | C25804
10uF Cap | C5 | 805 | C15850
10uF Cap | C6 | 805 | C15850
200R Res | R18 | 603 | C22962
200R Res | R19 | 603 | C22962
200R Res | R20 | 603 | C22962
200R Res | R21 | 603 | C22962
200R Res | R22 | 603 | C22962
200R Res | R23 | 603 | C22962
200R Res | R24 | 603 | C22962
200R Res | R25 | 603 | C22962
200R Res | R26 | 603 | C22962
200R Res | R27 | 603 | C22962
18pF Cap | C12 | 603 | C1647
18pF Cap | C13 | 603 | C1647
1uF Cap | C2 | 603 | C15849
1uF Cap | C10 | 603 | C15849
1uF Cap | C15 | 603 | C15849
1uF Cap | C16 | 603 | C15849
2.2uF Cap | C1 | 603 | C23630
2.2uF Cap | C3 | 603 | C23630
2.2uF Cap | C17 | 603 | C23630
330R Res | R13 | 603 | C23138
330R Res | R14 | 603 | C23138
330R Res | R15 | 603 | C23138
330R Res | R16 | 603 | C23138
330R Res | R17 | 603 | C23138
22R Res | R28 | 603 | C22962
22R Res | R29 | 603 | C22962
22uF Cap | C9 | 603 | C59461
22uF Cap | C18 | 603 | C59461
22uF Cap | C19 | 603 | C59461
3.3k Res | R3 | 603 | C22978
3.3k Res | R4 | 603 | C22978
3.3uH Ind | L1 | 603 | C408336
499k Res | R5 | 603 | C26751
56.2k Res | R10 | 603 | C23080
5m Res | R7 | 2512 | C49483
8MHz Crystal | Y1 | SMD-5032_2P | C115962
atmega32u4 uP | U3 | TQFP-44_10.0x10.0x0.8P | C44854
bq769209 bmic | U1 | TSSOP-20_4.4x6.5x0.65P | C181647
NMOS | M1 | VSONP-8_EP_3.2x3.3x0.65P | C201632
Schottkey Diode | D2 | SOD-123FL | C191986

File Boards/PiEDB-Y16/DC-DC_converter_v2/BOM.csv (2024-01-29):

Comment | Designator | Footprint | JLCPCB Part #
TPS56C230RJER | U1 | TPS56C230RJER | C1849534
110k | R1 | R_0603_1608Metric | C728625
15k | R2 | R_0603_1608Metric | C336845
100k | R3, R6 | R_0402_1005Metric | C25741
200k | R4 | R_0402_1005Metric | C25764
33k | R5 | R_0402_1005Metric | C25779
51k | R7 | R_0402_1005Metric | C25794
1uF | C1 | C_0805_2012Metric | C28323
0.1uF | C2, C5 | C_1206_3216Metric | C24497
22uF | C3, C4 | C_1206_3216Metric | C12891
47uF | C6, C7, C8, C9 | C_1206_3216Metric | C96123
1.8uH | L1 | 125CDMCCDS-1R8MC | C2453926
 | U2,U3 | anderson_horizontal

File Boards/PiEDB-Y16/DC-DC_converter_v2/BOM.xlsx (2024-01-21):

Comment | Designator | Footprint | JLCPCB Part # | Value
TPS56C230RJER | U1 |  | C1849534
RT0603DRE07110KL | R1 | 0603 | C728625 | 110kΩ
ERJ3RBD1502V | R2 | 0603 | C336845 | 15kΩ
CQ02WGJ0104TCE | R3 | 0402 | C966710 | 100kΩ
CR0402-JW-184GLF | R4 | 0402 | C203132 | 180kΩ
RMC10-333JTH | R5 | 0402 | C323721 | 33kΩ
FRC0402J913 TS | R6 | 0402 | C2906973 | 91kΩ
SY0402JN47KP | R7 | 0402 | C380748 | 47kΩ
CL21A105KACLNNC | C1 | 0805 | C2932475 | 1uF
C1206X104K251T | C2, C5 | 1210 | C106024 | 0.1uF
TMK316BBJ226ML-T | C3, C4 | 1210 | C386093 | 22uF
 | C6, C7, C8, C9 | 1210 |  | 47uF
NL0805B103J500CPBN | C10 | 0805 | C841540 | 10nF
C0603N101K251T | C11 | 0402 | C961506 | 110pF

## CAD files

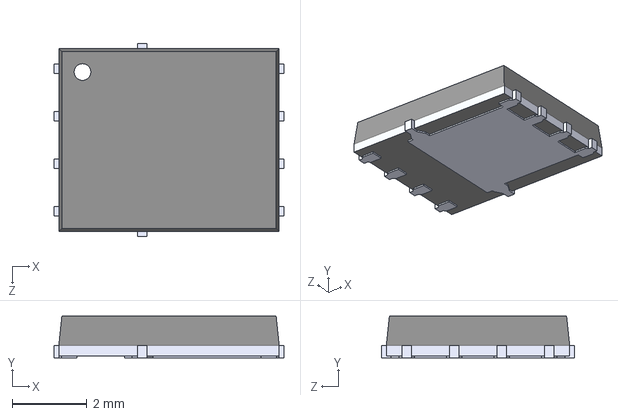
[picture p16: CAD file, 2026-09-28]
Boards/PiEDB-Y17/gabesam board/3DModels/SI7149ADP-T1-GE3.STEP
6.15 x 1.12 x 5.16 mm

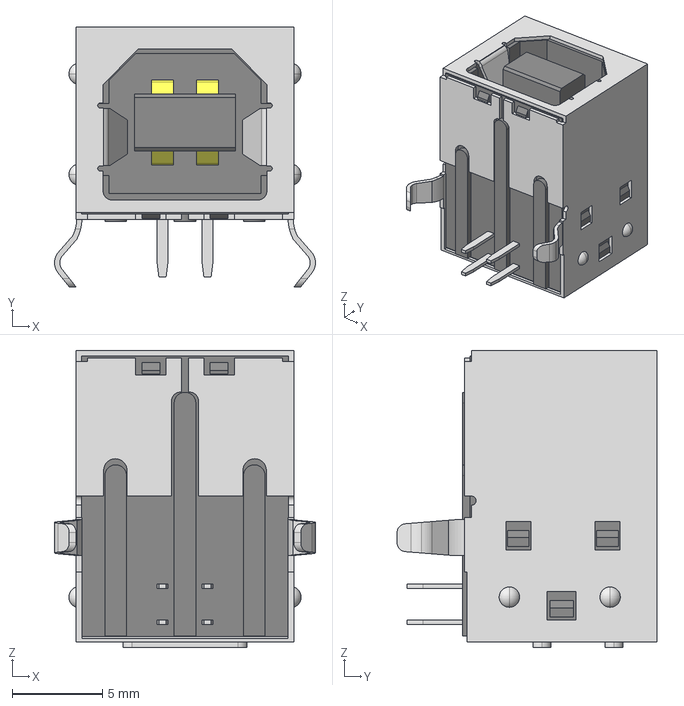
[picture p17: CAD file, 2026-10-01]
Boards/PiEDB-Y19/PDB/3DModels/USB-B-S-S-B-TH.stp
14.5 x 14.4 x 16.5 mm

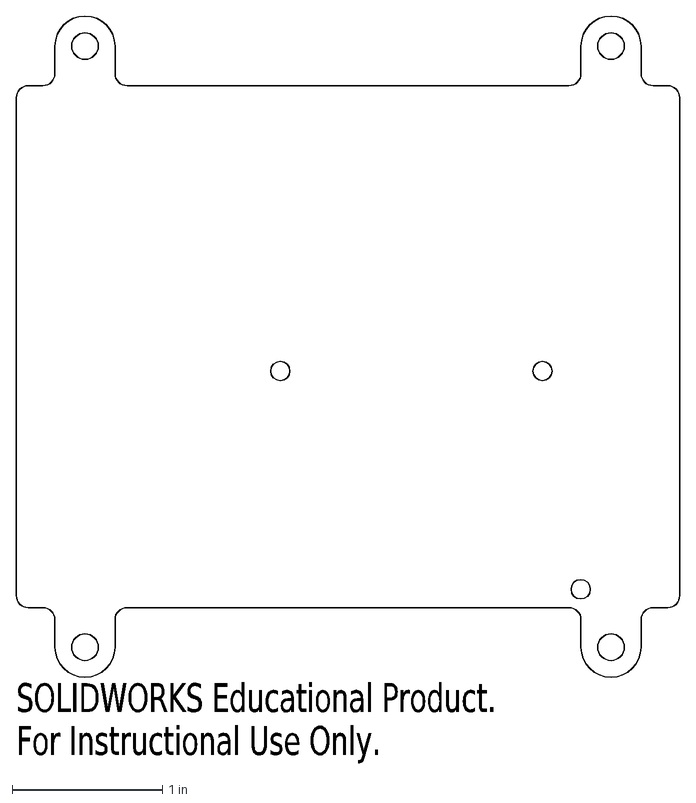
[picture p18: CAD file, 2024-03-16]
Enclosures/Y16/PDBBottom.DXF
SOLIDWORKS Educational Product.
For Instructional Use Only.

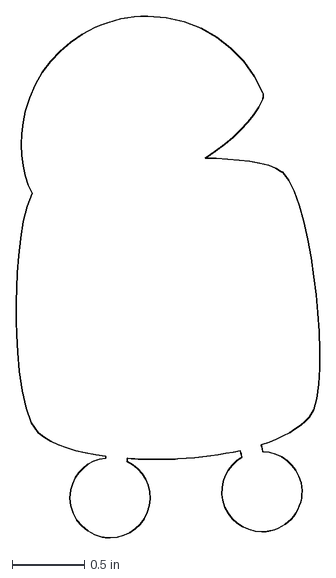
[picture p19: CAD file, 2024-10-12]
Onboarding/Y17/Turbo PCB Design/Turbo Image DXF files/Turbo-Body-PCB-PL.dxf
2.11 x 3.62 in

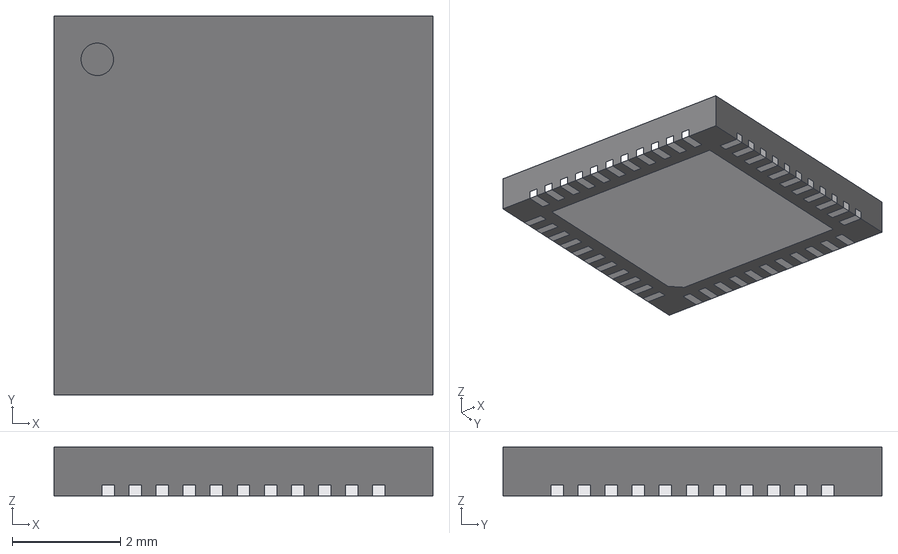
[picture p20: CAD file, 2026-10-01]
Boards/PiEDB-Y19/PDB/3DModels/ATmega32U4_QFN-44-1EP_7x7mm_P0.5mm_EP5.2x5.2mm.step
7.00 x 7.00 x 0.9 mm
pads
exposed_pad

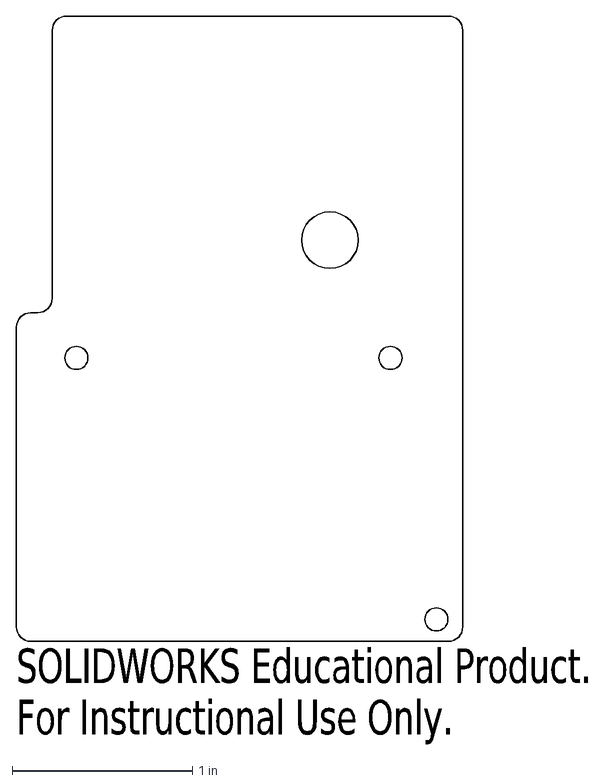
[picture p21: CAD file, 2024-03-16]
Enclosures/Y16/PDBTop.DXF
SOLIDWORKS Educational Product.
For Instructional Use Only.

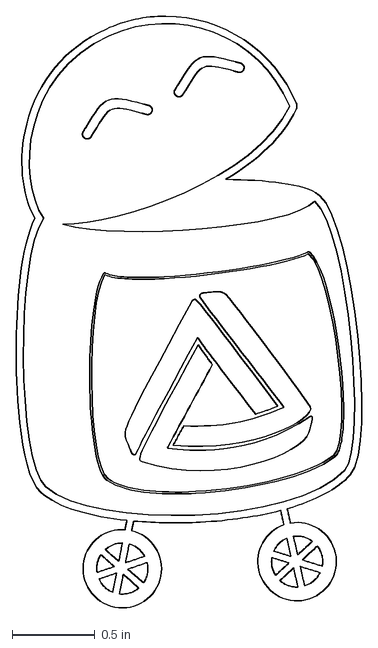
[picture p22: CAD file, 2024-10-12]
Onboarding/Y17/Turbo PCB Design/Turbo Image DXF files/Turbo-Body-silk-PL.dxf
2.09 x 3.57 in

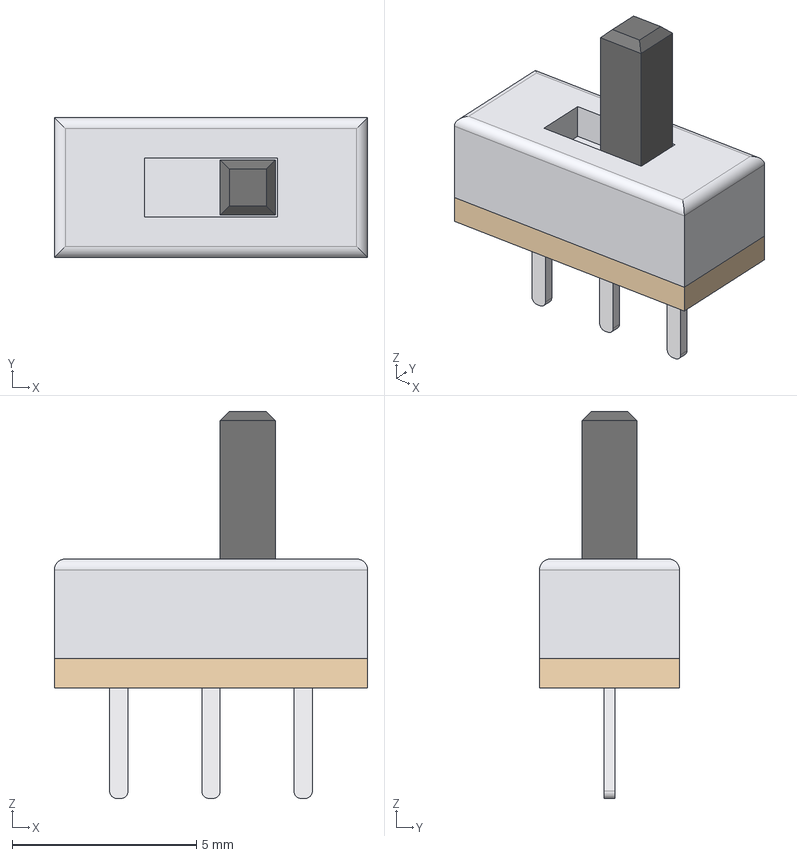
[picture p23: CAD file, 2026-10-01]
Boards/PiEDB-Y19/PDB/3DModels/SS-12D01-G4.step
8.50 x 3.80 x 10.5 mm
base
frame
knob
pins

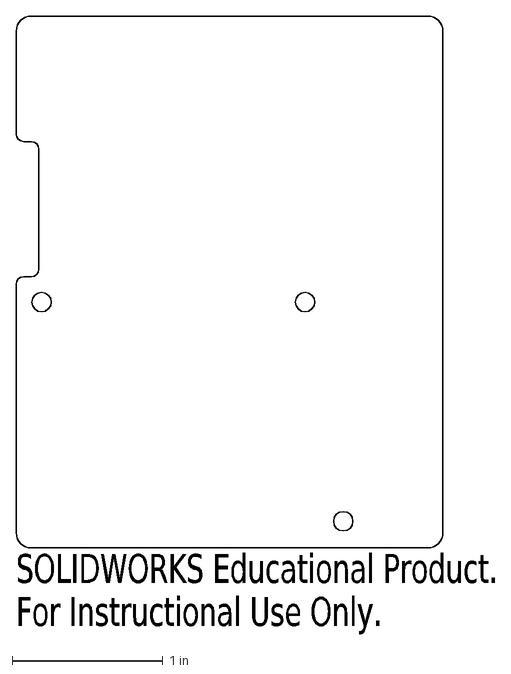
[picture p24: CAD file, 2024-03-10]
Enclosures/Y16/PDB_Enclosure_Top.DXF
SOLIDWORKS Educational Product.
For Instructional Use Only.

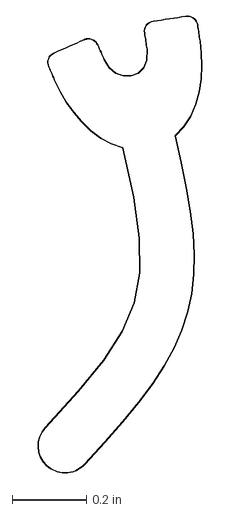
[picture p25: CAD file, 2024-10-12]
Onboarding/Y17/Turbo PCB Design/Turbo Image DXF files/Turbo-Arm-PCB-PL.dxf
0.44 x 1.23 in

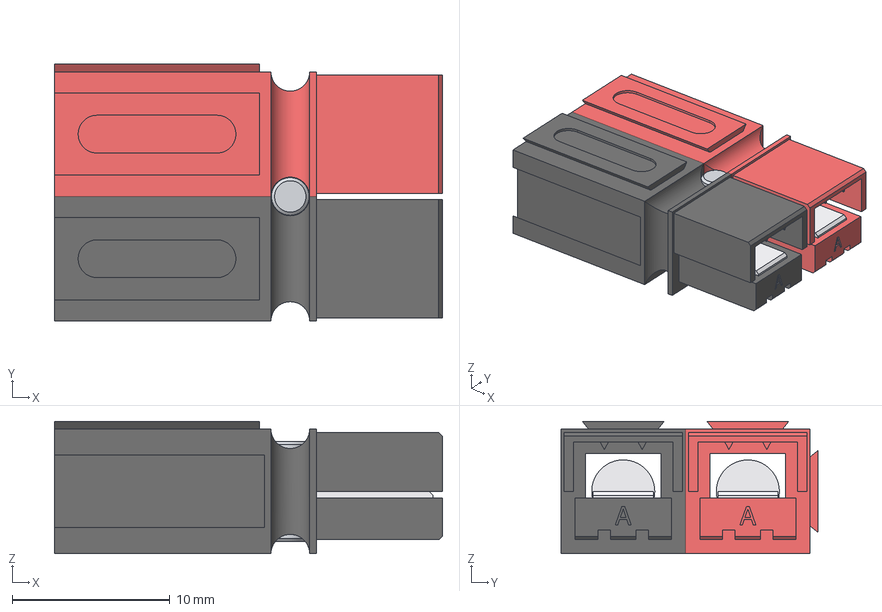
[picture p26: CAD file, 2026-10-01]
Boards/PiEDB-Y19/PDB/3DModels/Powerpole_PP45_red_black_pair.step
24.6 x 16.3 x 8.40 mm
housing_red
housing_black
contact_pos
contact_neg
retaining_pin

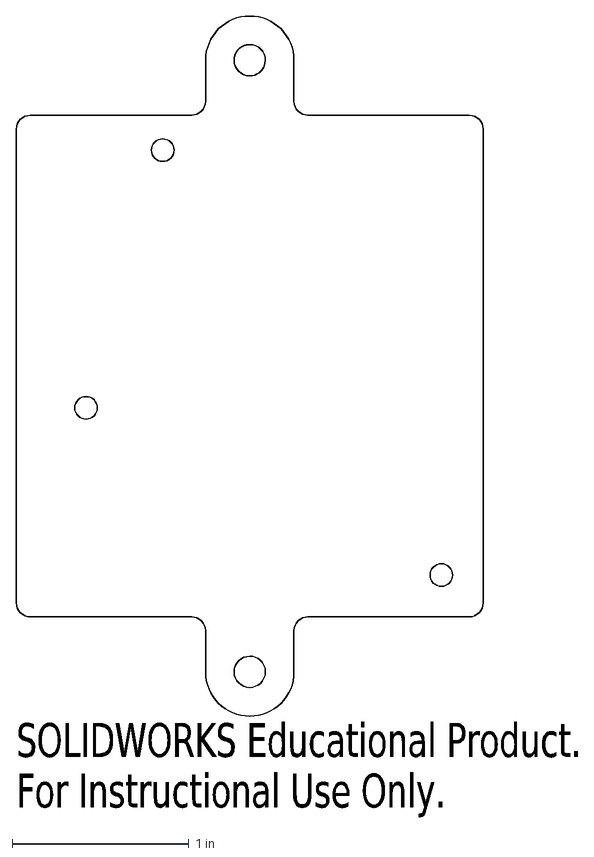
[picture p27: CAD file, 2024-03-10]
Enclosures/Y16/Motor_Enclosure_Bottom.DXF
SOLIDWORKS Educational Product.
For Instructional Use Only.

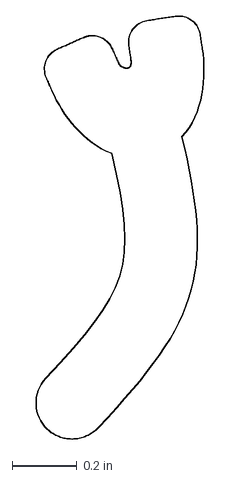
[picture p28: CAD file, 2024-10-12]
Onboarding/Y17/Turbo PCB Design/Turbo Image DXF files/Turbo-Arm-PCB-PL+1mm.dxf
0.519 x 1.31 in

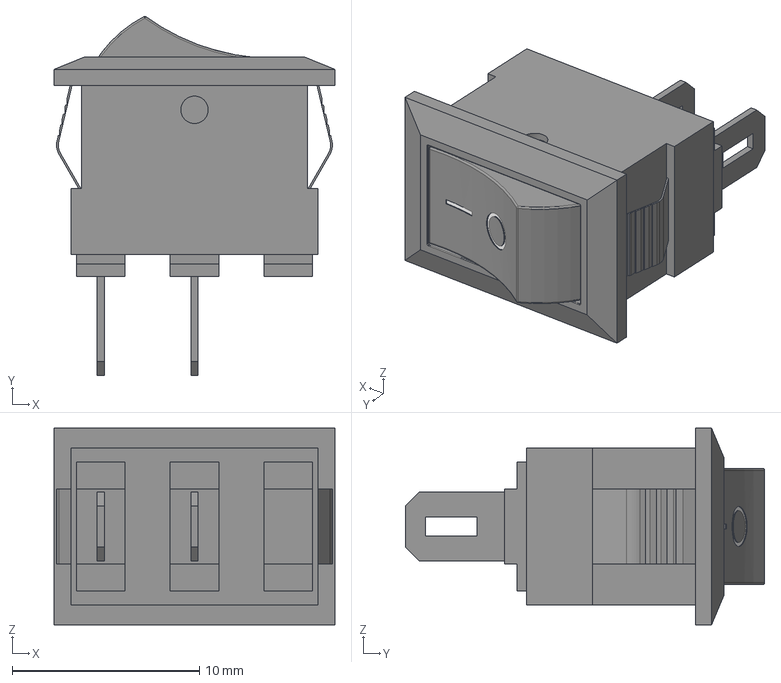
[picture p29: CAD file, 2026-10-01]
Boards/PiEDB-Y19/PDB/3DModels/SW-R3-1A-A-XX-0_black.step
15.0 x 19.2 x 10.5 mm

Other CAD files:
Enclosures/Y16/ServoControl_top.DXF
Onboarding/Y17/Turbo PCB Design/Turbo Image DXF files/Turbo-Body-PCB-PL+1mm.dxf
Boards/PiEDB-Y19/PDB/3DModels/FIT0587.stp
Enclosures/Y16/PDB_Enclosure_Bottom.DXF
Boards/PiEDB-Y17/gabesam board/3DModels/LM25085QMY_NOPB.step
Boards/PiEDB-Y19/PDB/3DModels/Buck_Converter_5V.step
Boards/PiEDB-Y19/PDB/3DModels/SFN-1207P7.6_buzzer.step
Boards/PiEDB-Y19/PDB/3DModels/SR410361N.step
Boards/PiEDB-Y19/PDB/3DModels/XF-508PVS-A_with_ATOF_10A.step
Enclosures/Y16/Motor_Enclosure_Top.DXF
Enclosures/Y16/Raspberry Pi Enclosure, Bottom.DXF
Enclosures/Y16/Raspberry Pi Enclosure, Top.DXF
Enclosures/Y16/ServoControl_bottom.DXF
Onboarding/Y17/Turbo PCB Design/Turbo Image DXF files/Turbo-Arm-silk-PL.dxf

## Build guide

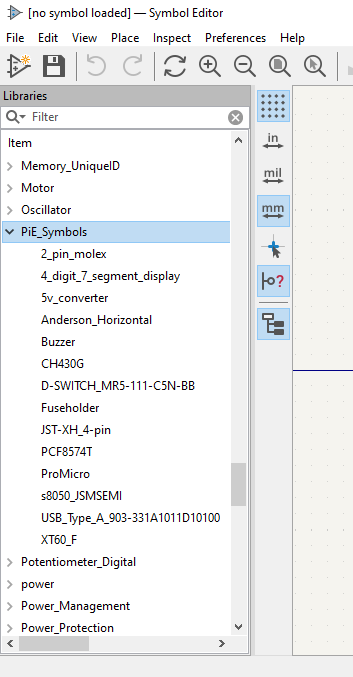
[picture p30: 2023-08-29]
Images/KiCad_Setup/symbol_setup6.png

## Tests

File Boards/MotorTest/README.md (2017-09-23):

# Testing Motor Controllers

Oscope Setup:

1. Turn on  Oscope
1. You'll need 4 probes
1. Hit `Utility` on the right side
1. Hit `File Explorer` on the bottom left of the screen
1. Use the `Push the select` scroller to select `setup_0.scp : Feb-19-2017` and hit `Load File` on the bottom left of the screen
1. Hook up the resistor-anderson to the moto side of the testing board
1. Hook up all `Ground` wires for the oscope probes to the `GND` wire from the testing board.
1. Attach `1` Oscope probe to `PWM` coming out of the testing board
1. Attack `3` Oscope probe to the Black side of the resistor attachment
1. Attach `4` Oscope probe to the Red side of the resistor attachmet
1. From `PiECentral/hibike`, run `sudo python hibike_process.py` after attaching the arduino to your computer
1. Set the powersupply to `12V` and `5A` and attach output to the motor controller
1. Hit output on on the powersupply and watch the oscope for beautiful square waves.

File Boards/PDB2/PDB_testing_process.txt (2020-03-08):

1) visual inspection under microscope
2) apply 12V to andersons and test 5V regulator
	-make sure output doesn't go below 4.8V when current set to 2.9A
3) burn arduino bootloader
4) solder 1k resistors for bar display
5) connect cell tap and 12V
6) upload test code
7) check outputs of serial monitor
8) test 12V current output

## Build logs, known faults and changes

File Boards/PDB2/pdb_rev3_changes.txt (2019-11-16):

1) increase hold pad size on segment display
2) increase hold size on button
3) increase via size of buzzer 
4) use saftey gnd for 5V converter

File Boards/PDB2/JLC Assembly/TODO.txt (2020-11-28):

-switch nmos to something JLC has
-rerun stuff

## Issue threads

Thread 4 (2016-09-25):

Boards should have only vector fonts

tobinsarah, 2016-09-25:
Many have proportional font right now. Low priority, but vector prints better on silkscreen and so will be more legible, which is helpful for production. This will require fixes in both library packages and .brd files

Closed 2016-10-13.

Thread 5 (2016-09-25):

Mounting Holes

tobinsarah, 2016-09-25:
"Boards should have at least 2 4-40 mounting holes in opposite corners (use the STAND-OFF part). The horizontal/vertical distance between them must be a multiple of 0.25 inches. It is preferred that the distance from the edge is also a multiple of 0.25 inches, but this is not required. If not physically possible, add an extra "wing" to the board for a tooling hole."

Closed 2016-11-20.

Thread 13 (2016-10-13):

Silkscreen Edits

onibrow, 2016-10-13:
# General
- PiE Logo and Copyright is being covered
- Only vector fonts
# Battery Buzzer
# PDB
# RFID
# Servo
# Team Flag
# Twist It
- Screw terminal on wrong side of board
- Strange part number is on the board
# Yogi Bear

Closed 2016-11-20.

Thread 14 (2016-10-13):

Sourcing

onibrow, 2016-10-13:
# Battery Buzzer
# PDB
# RFID
# Servo
# Team Flag
# Twist It
- Not all it's components are accounted for in the BOM
# Yogi Bear

Closed 2016-11-11.

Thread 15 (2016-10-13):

Board Size

onibrow, 2016-10-13:
# Battery Buzzer
- Strangely large
- Lot's of dead space
# PDB
- REALLY big
- Look into shaving off bottom area?
# RFID
# Servo
# Team Flag
# Twist It
- Maybe try to linearize the layout: usb on one end, screw terminal on other, opposed to the 90 degree angle we have currently
# Yogi Bear

Closed 2016-11-20.

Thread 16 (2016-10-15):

Team Flag

onibrow, 2016-10-15:
The BLUE LED is leaking ever so slightly. Also Doug noted that we should not be using the ones from DigiKey.

onibrow, 2016-10-15:
The APM is the wrong config. It needs to be rotated and flipped. We really need to check them before we ship.

onibrow, 2016-10-15:
By flipping the position of the LED's, the leakage is minimized

Closed 2016-10-20.

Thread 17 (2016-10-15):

TwistIt Product Design

onibrow, 2016-10-15:
Add strain holes infront of the screw terminal. Maybe not put it on the back, and instead stream line it.

onibrow, 2016-10-15:
Resistors change form 330 -> 10K

Closed 2016-10-22.

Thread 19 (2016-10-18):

Library BOM

onibrow, 2016-10-18:
Add parts need to have their manufacturer, part number, supplier, supply number etc.

onibrow, 2016-10-23:
RFID: Inductor chips, limit switches, servos, pots, line followers

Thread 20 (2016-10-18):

Magnetic Sensor

onibrow, 2016-10-18:
Something that can sense magnetic fields

onibrow, 2016-10-23:
[Amazon](https://www.amazon.com/uxcell%C2%AE-Glass-Tube-Switches-15-20AT/dp/B00900PBQY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)

Closed 2016-10-25.

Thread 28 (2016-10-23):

ATX 5V Connectors

onibrow, 2016-10-23:
Replace servo's anderson with an ATX

onibrow, 2016-10-24:
[Datasheet](http://www.molex.com/pdm_docs/sd/015311026_sd.pdf)

Closed 2016-10-27.

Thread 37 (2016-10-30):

Twist it feedback

dHutchings, 2016-10-30:
Feedback on Rev 9B before ship.

1) Silkscreen for the screw terminals could use some changes.  The silkscreen labels should still be visible even after the terminals are soldered in place, so users can look @ the board to determine which terminal is which.

2) Schematic needs net labels to the right of the R1 thru R3

3) Just a question about the motor driver.  (Confirm: is [this the link](https://www.aliexpress.com/item/Free-Shipping-30A-Mini-VNH2SP30-Stepper-Motor-Driver-Monster-Moto-Shield-module-For-Arduino/32247122784.html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,searchweb201602_2,searchweb201603_1&btsid=da69fb98-fc00-470f-801d-594a49b774ae) to the motor driver?)

How is this thing mounted to the twistit?  It looks like they're both back-to-back.  Have we talked to enclosures about this?  Having the andresons going out the back will make for a very... interesting... enclosure.

Although, tbh, i can't immediately think of a better way to do it.

onibrow, 2016-10-31:
Cool, fixed everything. The mounting has been thought about with Aravind, its the best we can get. Thanks again Doug!

Closed 2016-10-31.

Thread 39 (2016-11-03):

Redo part numbering on battery buzzer

dHutchings, 2016-11-03:
It's currently very sloppy

U$1 for the XT60
R0 because you didn't want to renumber everything
U1 (TI Chip) vs UC1 (arduino)
Andersons have "Conn" heading, not "JP"

Closed 2017-02-09.

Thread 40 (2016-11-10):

Team Flag SMD

onibrow, 2016-11-10:
The team flag's APM needs to be replaced by the surface mount one

Closed 2016-11-11.

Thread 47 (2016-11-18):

PDB Rev 9B erratta

dHutchings, 2016-11-18:
This is the list of PDB rev 9B erratta as currently discovered by Doug.  There may be more out there:
Erratta:
1. Wrong diameter holes (#10-32, should be #8-32) are used on the PCB for the DC converter
2. Footprint for the circuit breaker has issues:
-the footprint is symmetric, and it shouldn't be because the circuit breaker itself isn't
-the bottom hole needs more exposed copper to make soldering / bolting easier.
3. The Buzzer pin isn't a PWM on the arduino, so the buzzer can't actually buz.  We need to swap the "Calib" and "Buzzer_Signal" lines on the arduino.
4. Really need better silkscreen for the buttons, and high precision resistors.  I pushed the wrong button several times.

Improvements:

1.  The arduino currently is directly hooked up to the 5V line.  There should be a fuse added.
2.  We can delete SJ1.  It's unneeded now.
3.  The calibration Button is to be replaced with a Jumper.  That way, a student won't be able to accidentally trigger it but PiE Staff can still quickly re-calibrate it.
4. mounting holes are weirdly located.  More importantly, it seems like there will be a * small * upper enclosure area around the battery buzzer circuits, and there currently aren't enough mounting points there.  Check with enclosure people as to the dimensions of the holes - they may need to be #4-40's.
5. Need mounting for COTS battery buzzer just in case.

dHutchings, 2016-11-18:
Addendum to improvements: The 5-V anderson (red on left) is backwards relative to the 12V rail.  The 12V rail is in compliance with our long-standing standards (AKA the grizzly).

There's talk of replacing the 5V andersons with some other kind of connector, idk, ask someone about that.  Either way, replace the connector, or fix the orientation.

dHutchings, 2016-11-18:
Need to add a 3.3k (ish?  maybe 10k) resistor between 5V and GND, to help with turn-off performance.

tobinsarah, 2016-11-22:
[] Wrong diameter holes (#10-32, should be #8-32) are used on the PCB for the DC converter
Footprint for the circuit breaker has issues:
[] the footprint is symmetric, and it shouldn't be because the circuit breaker itself isn't
[] the bottom hole needs more exposed copper to make soldering / bolting easier.
The Buzzer pin isn't a PWM on the arduino, so the buzzer can't actually buz. We need to swap the
[] "Calib" and "Buzzer_Signal" lines on the arduino.
[] Really need better silkscreen for the buttons, and high precision resistors. I pushed the wrong button several times.
Improvements:

[] The arduino currently is directly hooked up to the 5V line. There should be a fuse added.
[] We can delete SJ1. It's unneeded now.
[x] The calibration Button is to be replaced with a Jumper. That way, a student won't be able to accidentally trigger it but PiE Staff can still quickly re-calibrate it.
[] mounting holes are weirdly located. More importantly, it seems like there will be a * small * upper [] enclosure area around the battery buzzer circuits, and there currently aren't enough mounting points there. Check with enclosure people as to the dimensions of the holes - they may need to be #4-40's.
[] Need mounting for COTS battery buzzer just in case.

dHutchings, 2016-11-22:
Updated list:

Schematic:
-Did not add Buzzer-disabling jumper.  (Nor changed the resistor values)
-Almost every resistor on the schematic is missing its value label.
-Wrong part for APM fuse.  The fuse part is currently wrong in the schematic (it's a jumper.  It should be a fuse)
-Rename "Calibration Button" to "Calibration Jumper"
-This PDB design is using anderson connectors for the 5V rail.  According to Seiya, these were supposed to be switched to ATX connectors.  He'll know which polariy convention to follow.
-Didn't add mounting for COTS battery buzzer.

Routing
-Use Round Vias, not square ones
-Don't need trage for GND for JP2.  Should work fine without that trace, because ground planes.
-Location of R17 isn't logical.  It'd make sense to keep it somewhere near the Power Regulator, not hanging out in the middle of the Battery Buzzer.
-Looks like circuit breaker is still symmetrical.  However, the real circuit breaker isn't.

Silkscreen:
It looks much better, but could still use some work:

-7-segment label is proportional, not vector font.  Could also be bigger.
-Same for "LED 2" label
-Could use a label next to JP2 telling what it is
-Draw a box around R2 thru R7.  Then label the box "High Precision"
-The silkscreen on the fuses is offset.  On some fuses, the label is to the left.  On others, it's to the right.

Closed 2016-12-08.

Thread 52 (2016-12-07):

Team Flag Footprint

onibrow, 2016-12-07:
Arduino pro micro footprint needs to be flipped on one side

Closed 2016-12-08.

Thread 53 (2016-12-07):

ATX

onibrow, 2016-12-07:
ATX Footprint is too small

Closed 2016-12-08.

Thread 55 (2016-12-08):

Minor PDB erratta, mostly silksreen

dHutchings, 2016-12-08:
- [x] Include "+" on the anderson & ATX connectors to allow for correct installation of andersons w/out looking it up
- [x] Update ATX connector to new footprint.
- [ ] Add Nuts & Bolts to BOM.

dHutchings, 2017-01-05:
Molex Connectors are named JP's but the Andersons are named conn's?
Molex connector part doesn't have a silkscreen name associated with it intrinsically.
Molex connectors named JPs are causing other cumpers (JP7, JP8 to have large numbers)
Calib_jumper should be renamed to JP9.  (and, why do we have 3 different parts for 2 pin jumpers?  beyond me).

dHutchings, 2017-01-05:
- [ ]  The wire thicknesses for the wires around S1 are a little wierd (although all will work).  It doesn't matter anyway, since S1 is a DNP.

Closed 2017-02-09.

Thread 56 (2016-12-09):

Screw Terminals

onibrow, 2016-12-09:
smol

dHutchings, 2017-02-08:
?  Is this the hole diameter or something else?  Cause i fixed the hole diameters.

Closed 2017-02-22.

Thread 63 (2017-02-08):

Twist it fixes for yogibear

dHutchings, 2017-02-08:
Running list of fixes for yogibear for next year:

Enable falls from 4.65 (VCC) to 4.5 V when entering an error state.  The amount the voltage falls is set by a resistive network on the motor driver chip, i.e. something that we can't change.  However, this change in voltage is readable from an ADC:
- [x] Connect the "EN" pin to an ADC - capable Arduino Pro Micro pin.

dHutchings, 2017-02-16:
- [ ] Change the pull-up value for the encoders to 1k.

dHutchings, 2017-02-27:
- [ ] Add the pull-ups for the encoders back.  Value should be as stated above.
- [ ] The form factor for the yogibear's red board leaves something to be desired.  Unique board-to-board connection strategies (AKA two right-angle .1" headers) may allow a flatter package.

dHutchings, 2017-02-27:
- [ ] Add the pull-ups for the encoders back.  Value should be as stated above.
- [ ] The form factor for the yogibear's red board leaves something to be desired.  Unique board-to-board connection strategies (AKA two right-angle .1" headers) may allow a flatter package.

onibrow, 2017-08-19:
Slide over the red board connector so the andersons can be soldered in straight up

Closed 2017-10-15.

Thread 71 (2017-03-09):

Servo:

dHutchings, 2017-03-09:
Update servo silkscreen with which one is servo 1 and servo 0 in hibike.

avekan33, 2017-09-21:
Note: Servo 0 is pin 5 and Servo 1 is pin 6

Closed 2017-09-21.

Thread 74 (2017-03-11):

Change DRC for bay area circuits

tobinsarah, 2017-03-11:
we keep getting board shorts.

So: bigger isolate, and bigger spacing for things in general.

Closed 2017-09-21.

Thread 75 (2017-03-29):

Fuses for PDB

dHutchings, 2017-03-29:
The XT60 connector requires a lot of force to remove.

Sometimes, users will press down on nearby tall fuses (the thermal reset ones) for leverage, and break the fuseholder in the process.

Closed 2017-10-15.

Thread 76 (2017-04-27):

Pull-up Network on TwistIt is screwing with the line followers

onibrow, 2017-04-27:
Make the pull up network before the resistors, aka a 2x3 resistor network.

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

Move the box on right to before the resistor.

onibrow, 2017-06-06:
This would entail making a 2x3 jumper part, sourcing it, and replacing it on the twistit board.

dHutchings, 2017-06-07:
The pull-ups aren't needed at all for the line followers.

AKA: If we correctly produced the Twist-its (If we knew when to DNP the resistors), we would not have had pull-up problems..

onibrow, 2017-06-07:
I think this is slightly wrong. We weren't using the pull ups for the line followers, as they were powered and produced their own value. The issue comes because the pull up network is interfacing at a node that **all three** read pins are semi connected to. The readings become poor when one of the sensors reads a high, causing a pull up to the other readings as their is no drain, effectively pulling up the entire network. The fix would be have the jumper connect the three terminals to the five volts, not have the a collection of the  terminals connect to the 5V which was the solution this year.

dHutchings, 2017-06-10:
Or, we can just DNP R1, R2, and R3.  That will fix the problem with the line followers (and was how we fixed it last year)

The original intent was that R1...3 would either be populated or not, depending on the needs of the specific sensor attached to the board.  This was not followed in production, and the original cause of the line follower's response tracking each other.

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

onibrow, 2017-06-11:
Ooooh i see thanks for that, I like that solution better.

Closed 2017-09-21.

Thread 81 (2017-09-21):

Make TwistIt smaller

avekan33, 2017-09-21:
This is probably included in some of Doug's issues, but I wanted to emphasize its position in the queue/stack. This is to enable andersons to go vertical on both sides.

dHutchings, 2017-09-22:
Actually I think I forgot to write this down on github, so TY for remembering!

IRRC, just sliding the connector over a bit would allow for both andersons to go vertical, but there may be something better out ther.

Also, this is actually brings up one other tweak:
- [ ] Ensure that the Encoder connectors are on the same side of the Yogibear as the Motor's output cable.  (It currently isn't, thus forcing wires to do crazy things)

Closed 2017-10-15.

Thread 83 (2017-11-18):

Rework redboard test jig with pogo pins

avekan33, 2017-11-18:
refer to Doug
1) test h bridge waveform
2) test current (1A, 2A, 5A) (I think?)

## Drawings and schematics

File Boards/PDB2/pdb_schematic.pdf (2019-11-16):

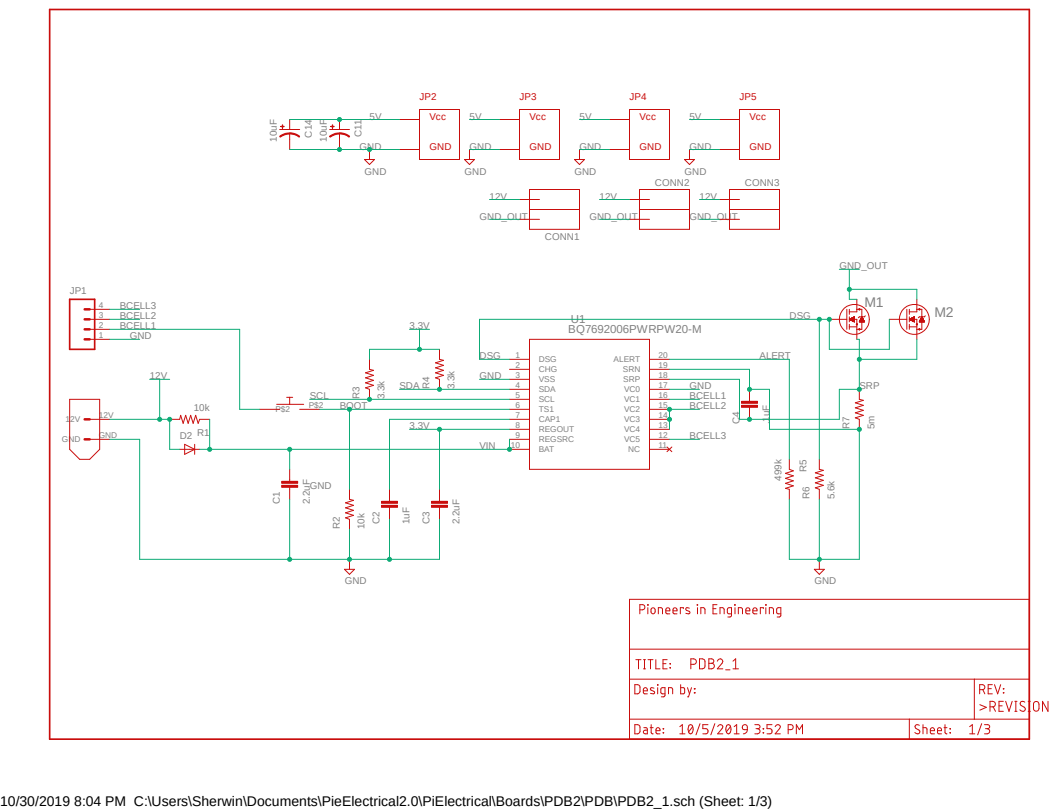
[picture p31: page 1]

10/30/2019 8:04 PM C:\Users\Sherwin\Documents\PieElectrical2.0\PiElectrical\Boards\PDB2\PDB\PDB2_1.sch (Sheet: 1/3)

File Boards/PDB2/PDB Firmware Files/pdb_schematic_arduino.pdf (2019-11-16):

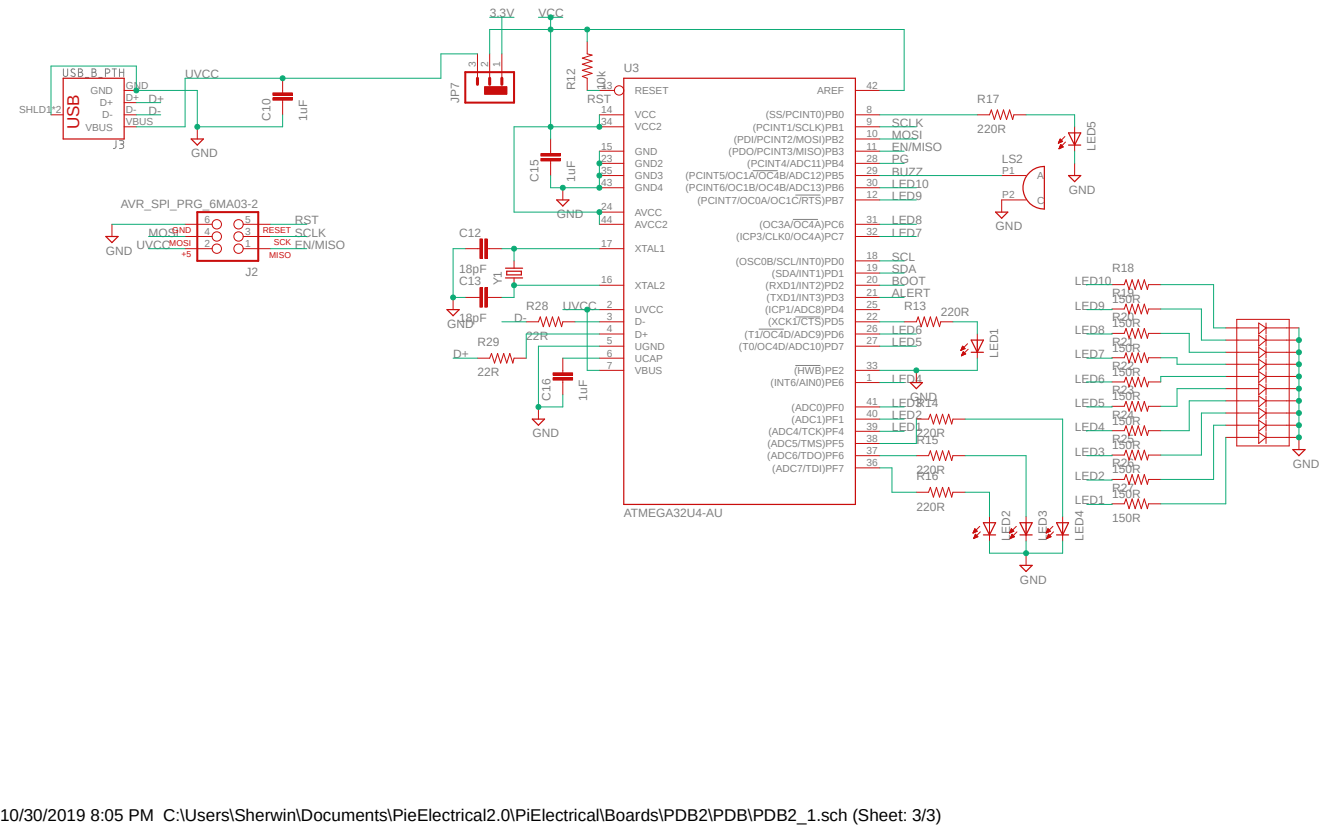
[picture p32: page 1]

10/30/2019 8:05 PM C:\Users\Sherwin\Documents\PieElectrical2.0\PiElectrical\Boards\PDB2\PDB\PDB2_1.sch (Sheet: 3/3)

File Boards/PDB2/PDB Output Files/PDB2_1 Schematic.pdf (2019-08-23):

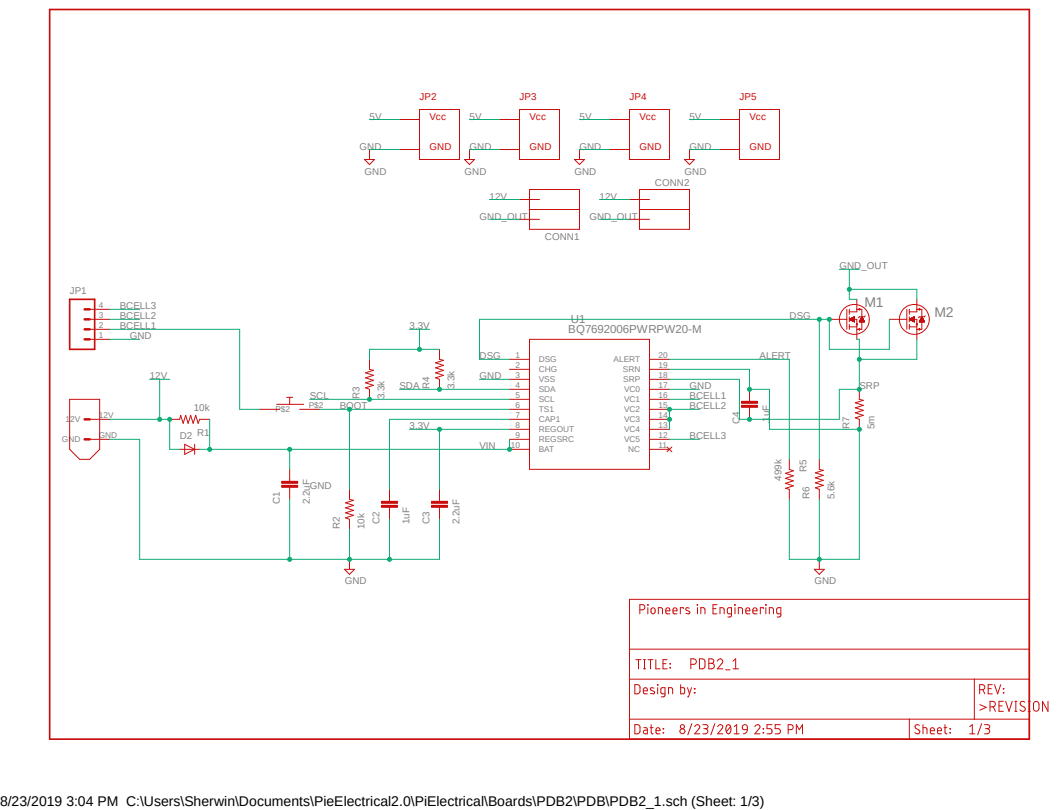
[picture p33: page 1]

8/23/2019 3:04 PM C:\Users\Sherwin\Documents\PieElectrical2.0\PiElectrical\Boards\PDB2\PDB\PDB2_1.sch (Sheet: 1/3)

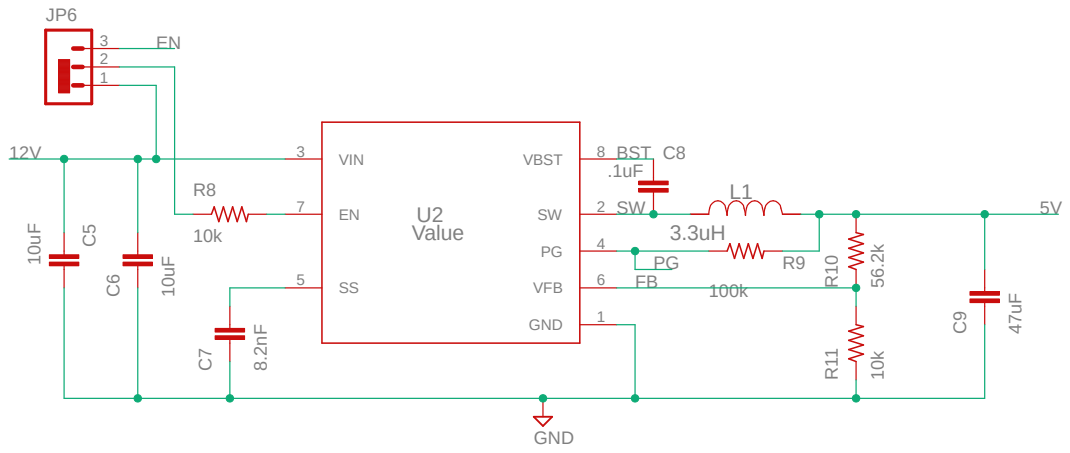
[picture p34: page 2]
Value; GND; 47uFC⁶; R9 R¹¹ R¹⁰ GND; 2 VIN 3; VFB; VBST; BST

8/23/2019 3:04 PM C:\Users\Sherwin\Documents\PieElectrical2.0\PiElectrical\Boards\PDB2\PDB\PDB2_1.sch (Sheet: 2/3) ¹⁰uF

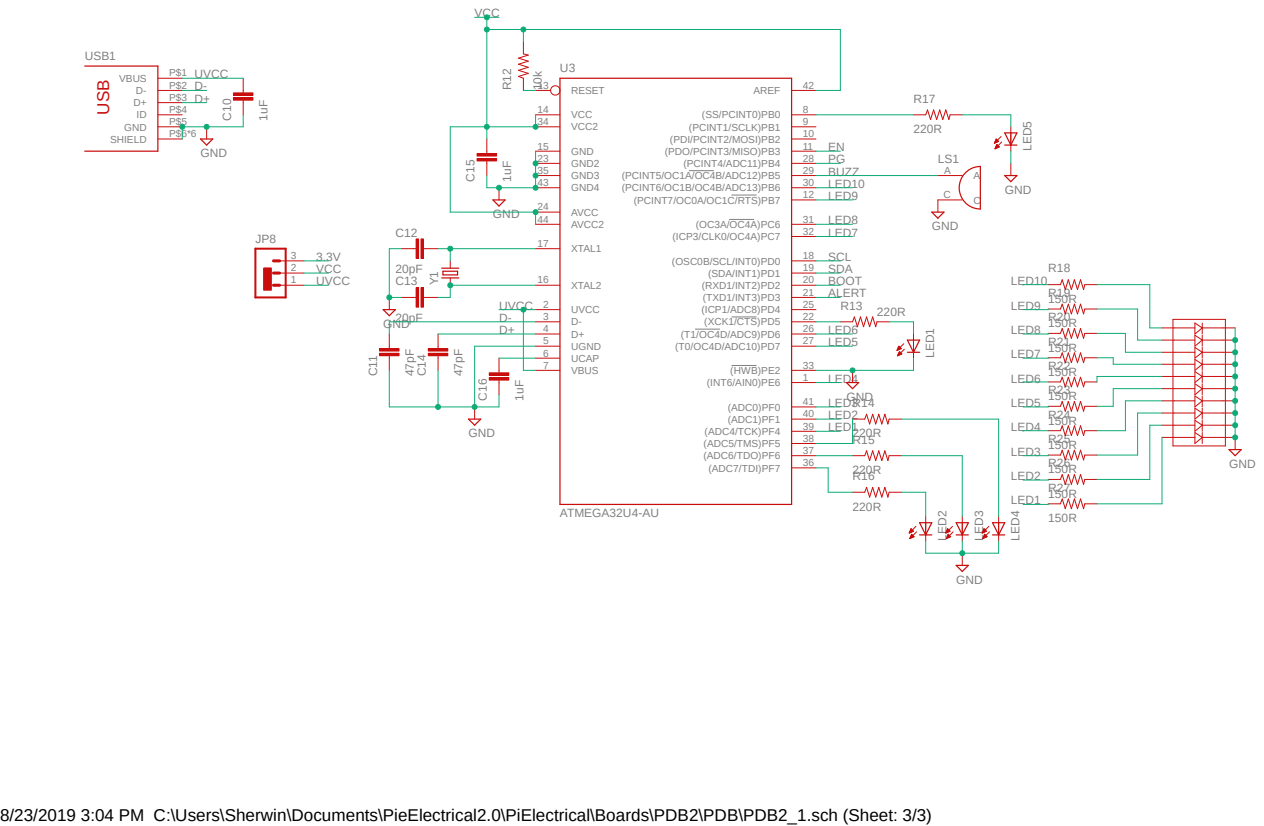
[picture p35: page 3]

8/23/2019 3:04 PM C:\Users\Sherwin\Documents\PieElectrical2.0\PiElectrical\Boards\PDB2\PDB\PDB2_1.sch (Sheet: 3/3)

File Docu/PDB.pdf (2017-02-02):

Battery & Circuit Breaker | 12V Rail | 5V Rail GND | GND GND | GND | GND GND | GND | GND GND GND GND GND | GND ¹²V | 12V GND | GND | VCC GND CONN2 VCC GND CONN1 | VCC GND CONN4 VCC GND CONN5 VCC GND CONN3 | VCC GND CONN6 | IN+ IN+ | OUT+ | OUT+ IN- IN- | OUT- | OUT- BUCK_CONVERTER_5V 12V 12V BAT | 12V | 5V GND Vcc CONN7 GND Vcc CONN8 | GND Vcc CONN9 GND Vcc CONN10

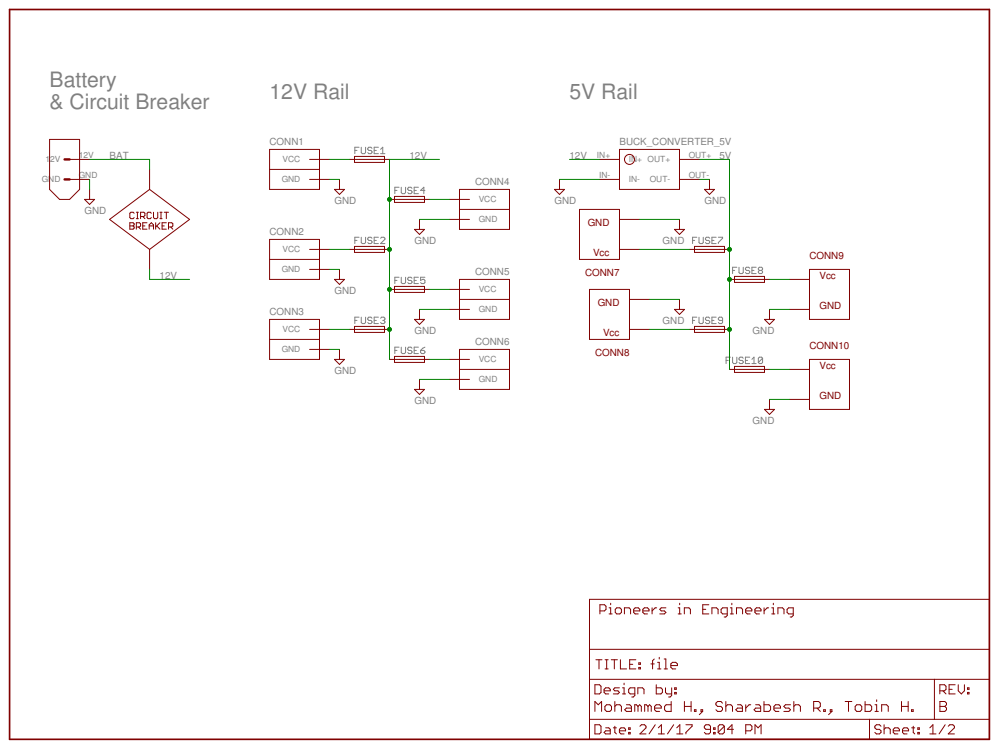
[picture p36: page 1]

### XH_CONN

1k | 100k | 5V

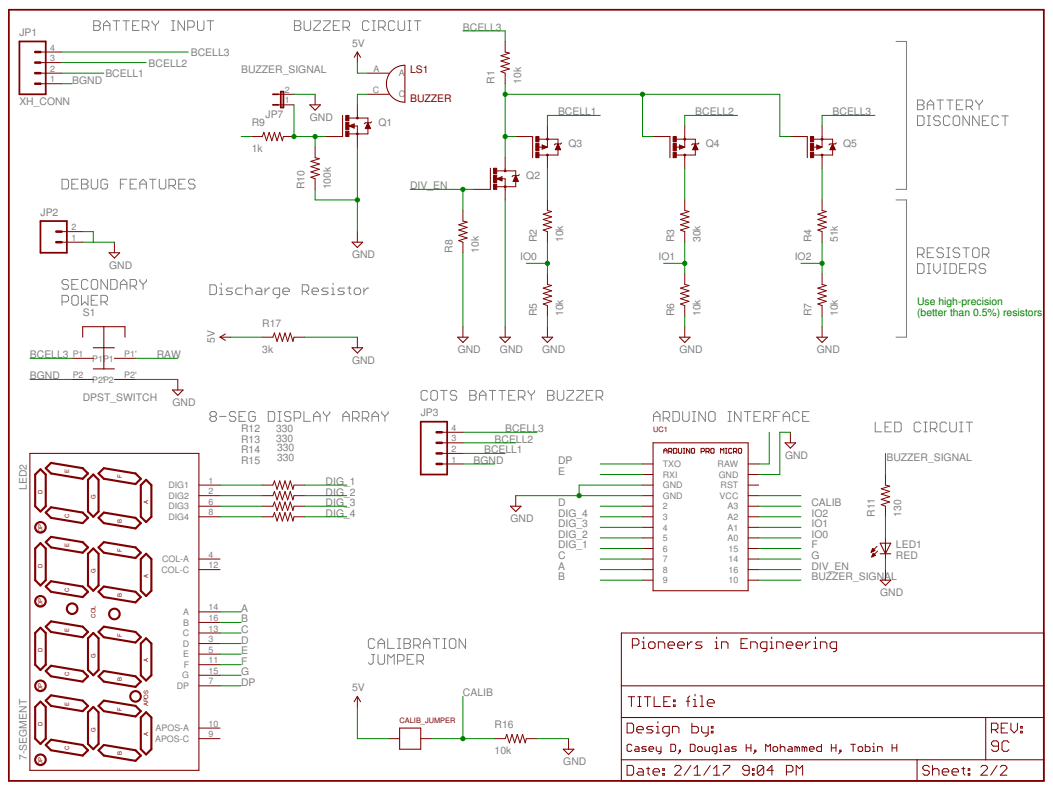
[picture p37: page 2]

+ | + | + | +
CONN - | - | - | - ⁷ | CONN9 | CONN8 | CONN10

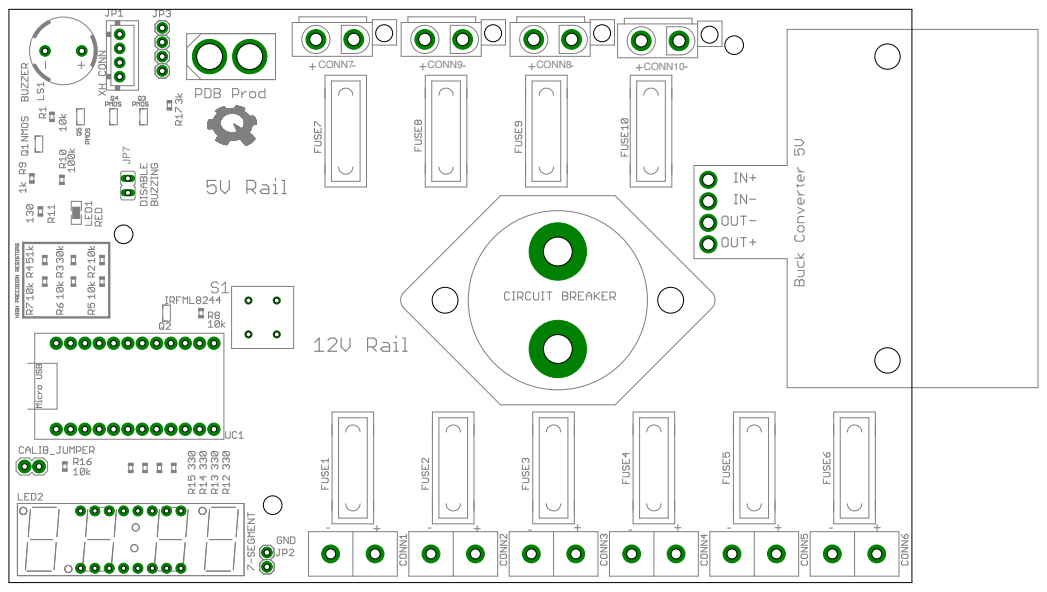
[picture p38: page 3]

+ | + | + | +
CONN - | - | - | - ⁷ | CONN9 | CONN8 | CONN10

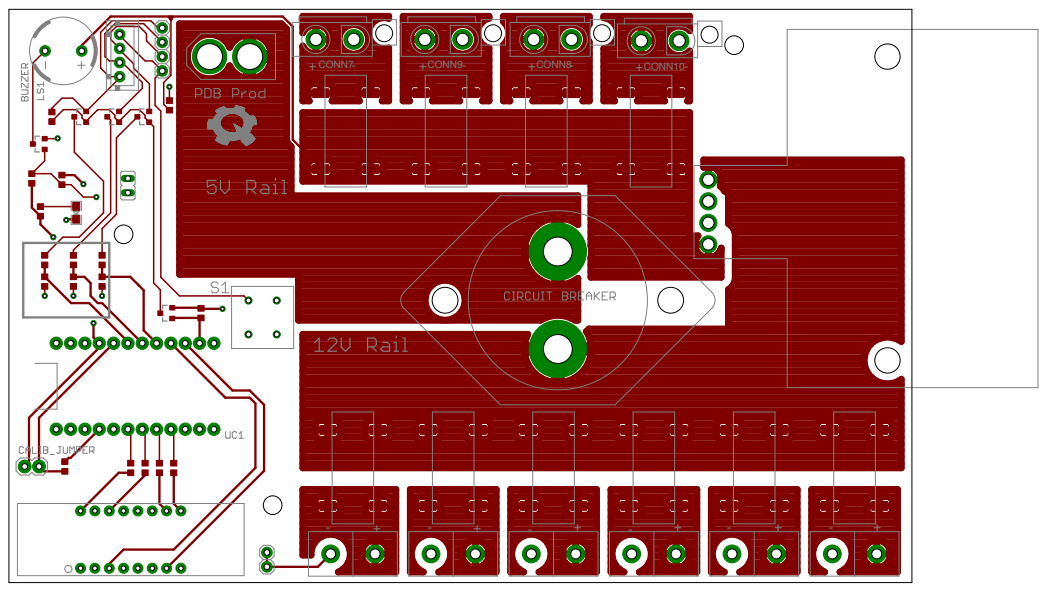
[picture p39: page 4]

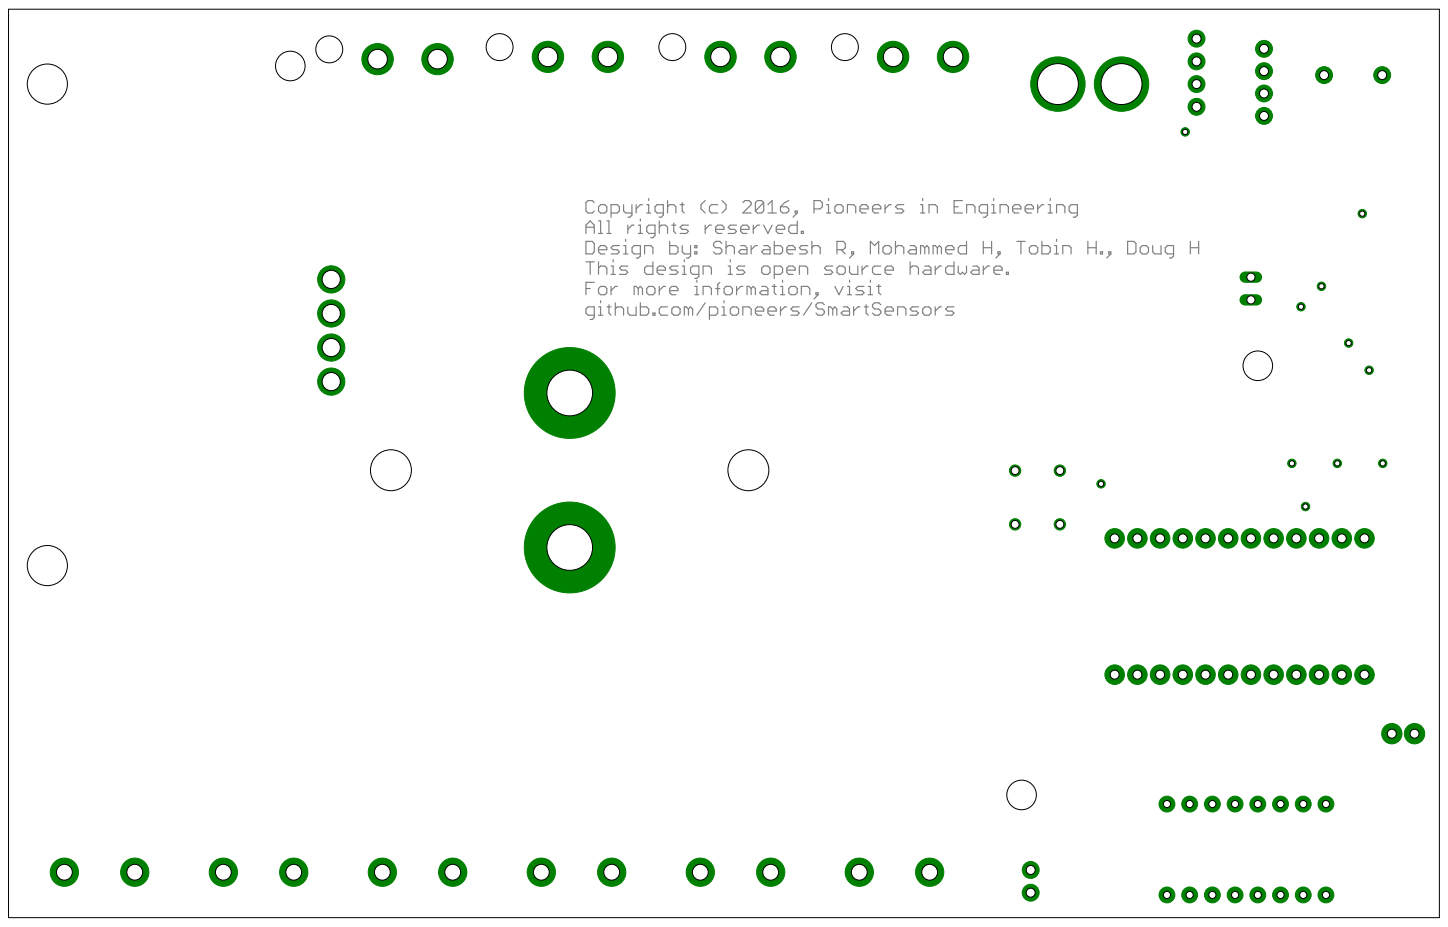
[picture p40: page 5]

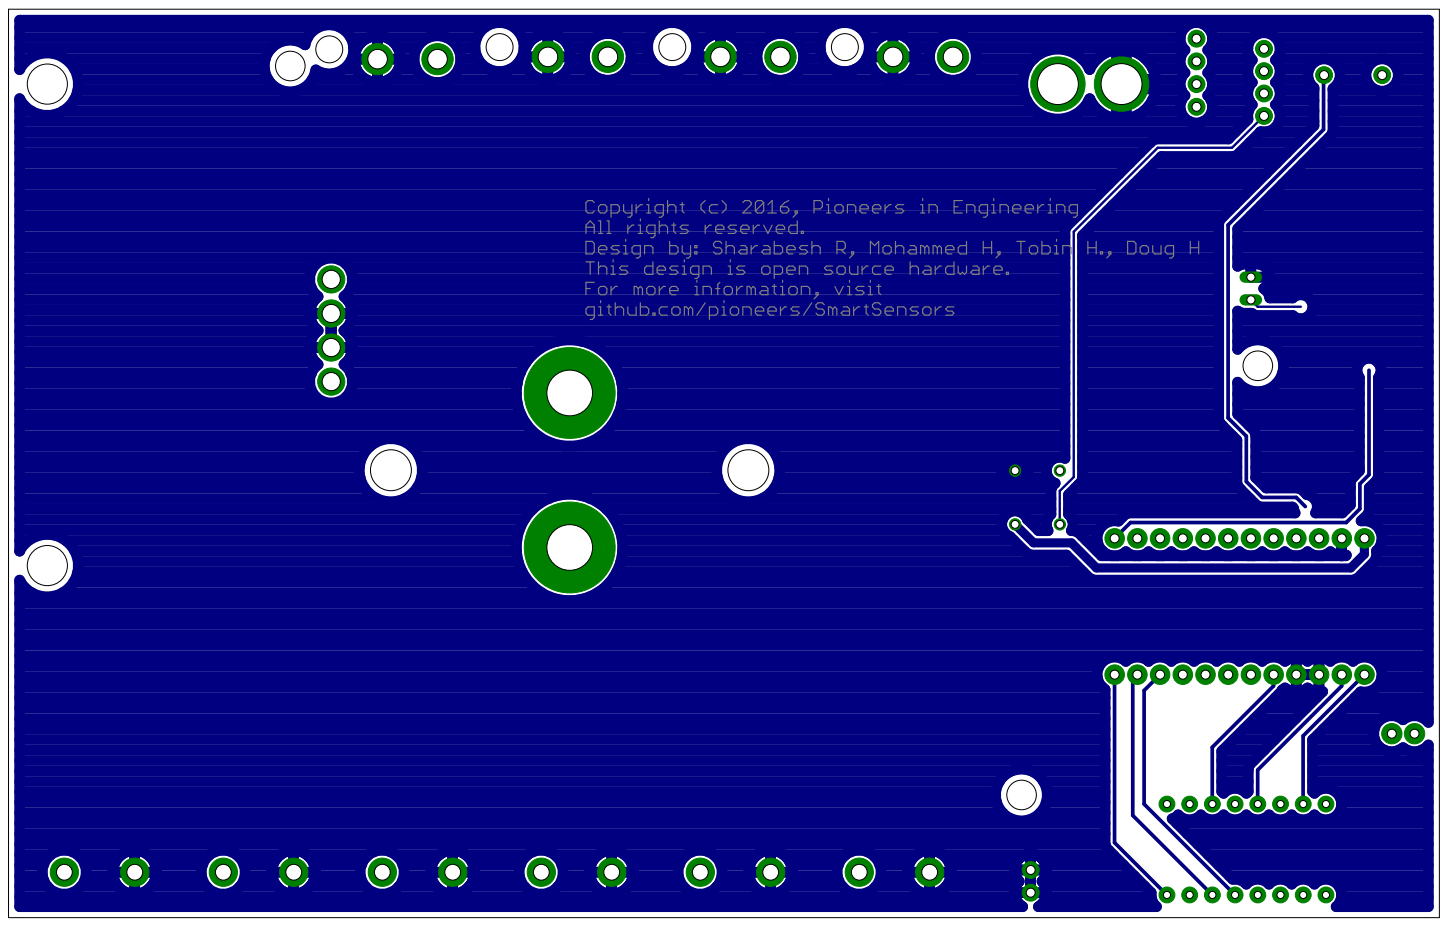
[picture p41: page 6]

Name | Value | Package | Notes | Ref Number
CALIB_JUMPER | JUMPER | JUMPER | 2 Pin Jumper
CIRCUIT_ BREAKER | CIRC_BREAKER | CIRC_BREAKER | PiE Circuit Breaker: product page
CONN1 | ANDERSONVERTICAL | ANDERSON_ VERTICAL | 2-pin 25A Anderson Connector | Anderson
CONN2 | ANDERSONVERTICAL | ANDERSON_ VERTICAL | 2-pin 25A Anderson Connector | Anderson
CONN3 | ANDERSONVERTICAL | ANDERSON_ VERTICAL | 2-pin 25A Anderson Connector | Anderson
CONN4 | ANDERSONVERTICAL | ANDERSON_ VERTICAL | 2-pin 25A Anderson Connector | Anderson
CONN5 | ANDERSONVERTICAL | ANDERSON_ VERTICAL | 2-pin 25A Anderson Connector | Anderson
CONN6 | ANDERSONVERTICAL | ANDERSON_ VERTICAL | 2-pin 25A Anderson Connector | Anderson
CONN7 | ATX | ATX | ATX 2 Pin Connector
CONN8 | ATX | ATX | ATX 2 Pin Connector
CONN9 | ATX | ATX | ATX 2 Pin Connector
CONN10 | ATX | ATX | ATX 2 Pin Connector
FUSE1 | FUSE_ HOLDER_SMD | FUSE_ HOLDER_SMD | ATC/ATO Fuse Holder. Original variant datasheet
FUSE2 | FUSE_ HOLDER_SMD | FUSE_ HOLDER_SMD | ATC/ATO Fuse Holder. Original variant datasheet
FUSE3 | FUSE_ HOLDER_SMD | FUSE_ HOLDER_SMD | ATC/ATO Fuse Holder. Original variant datasheet
FUSE4 | FUSE_ HOLDER_SMD | FUSE_ HOLDER_SMD | ATC/ATO Fuse Holder. Original variant datasheet
FUSE5 | FUSE_ HOLDER_SMD | FUSE_ HOLDER_SMD | ATC/ATO Fuse Holder. Original variant datasheet
FUSE6 | FUSE_ HOLDER_SMD | FUSE_ HOLDER_SMD | ATC/ATO Fuse Holder. Original variant datasheet
FUSE7 | FUSE_ HOLDER_SMD | FUSE_ HOLDER_SMD | ATC/ATO Fuse Holder. Original variant datasheet
FUSE8 | FUSE_ HOLDER_SMD | FUSE_ HOLDER_SMD | ATC/ATO Fuse Holder. Original variant datasheet
FUSE9 | FUSE_ HOLDER_SMD | FUSE_ HOLDER_SMD | ATC/ATO Fuse Holder. Original variant datasheet
FUSE10 | FUSE_ HOLDER_SMD | FUSE_ HOLDER_SMD | ATC/ATO Fuse Holder. Original variant datasheet
JP1 | XH_CONN | XH_ CONNECTOR_ 4POS_2.5MM | 4-pin XH connector (through-hole type shrouded
| | | header) | XH-4POS
JP2 | | 1X02 | 2-pin 0.1-inch header and MTA connector | BULK-STOCK
JP3 | | 1X04 | 4-pin 0.1-inch header and MTA connector | BULK-STOCK
JP7 | | JP1 | JUMPER
LED1 | RED | LED-0805 | LEDs | LED
LED2 | 7-SEGMENT | 7- SEGMENT- 4DIGIT- YOUNGSUN | This is a part for the 4-Digit 7-segment LEDs from Young Sun. Different from the Digikey LEDs, all 16 pins are used.
LS1 | BUZZER | BUZZER_ MAGNETIC_ 5V_12MM_RADIAL | Buzzer | BUZZER
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

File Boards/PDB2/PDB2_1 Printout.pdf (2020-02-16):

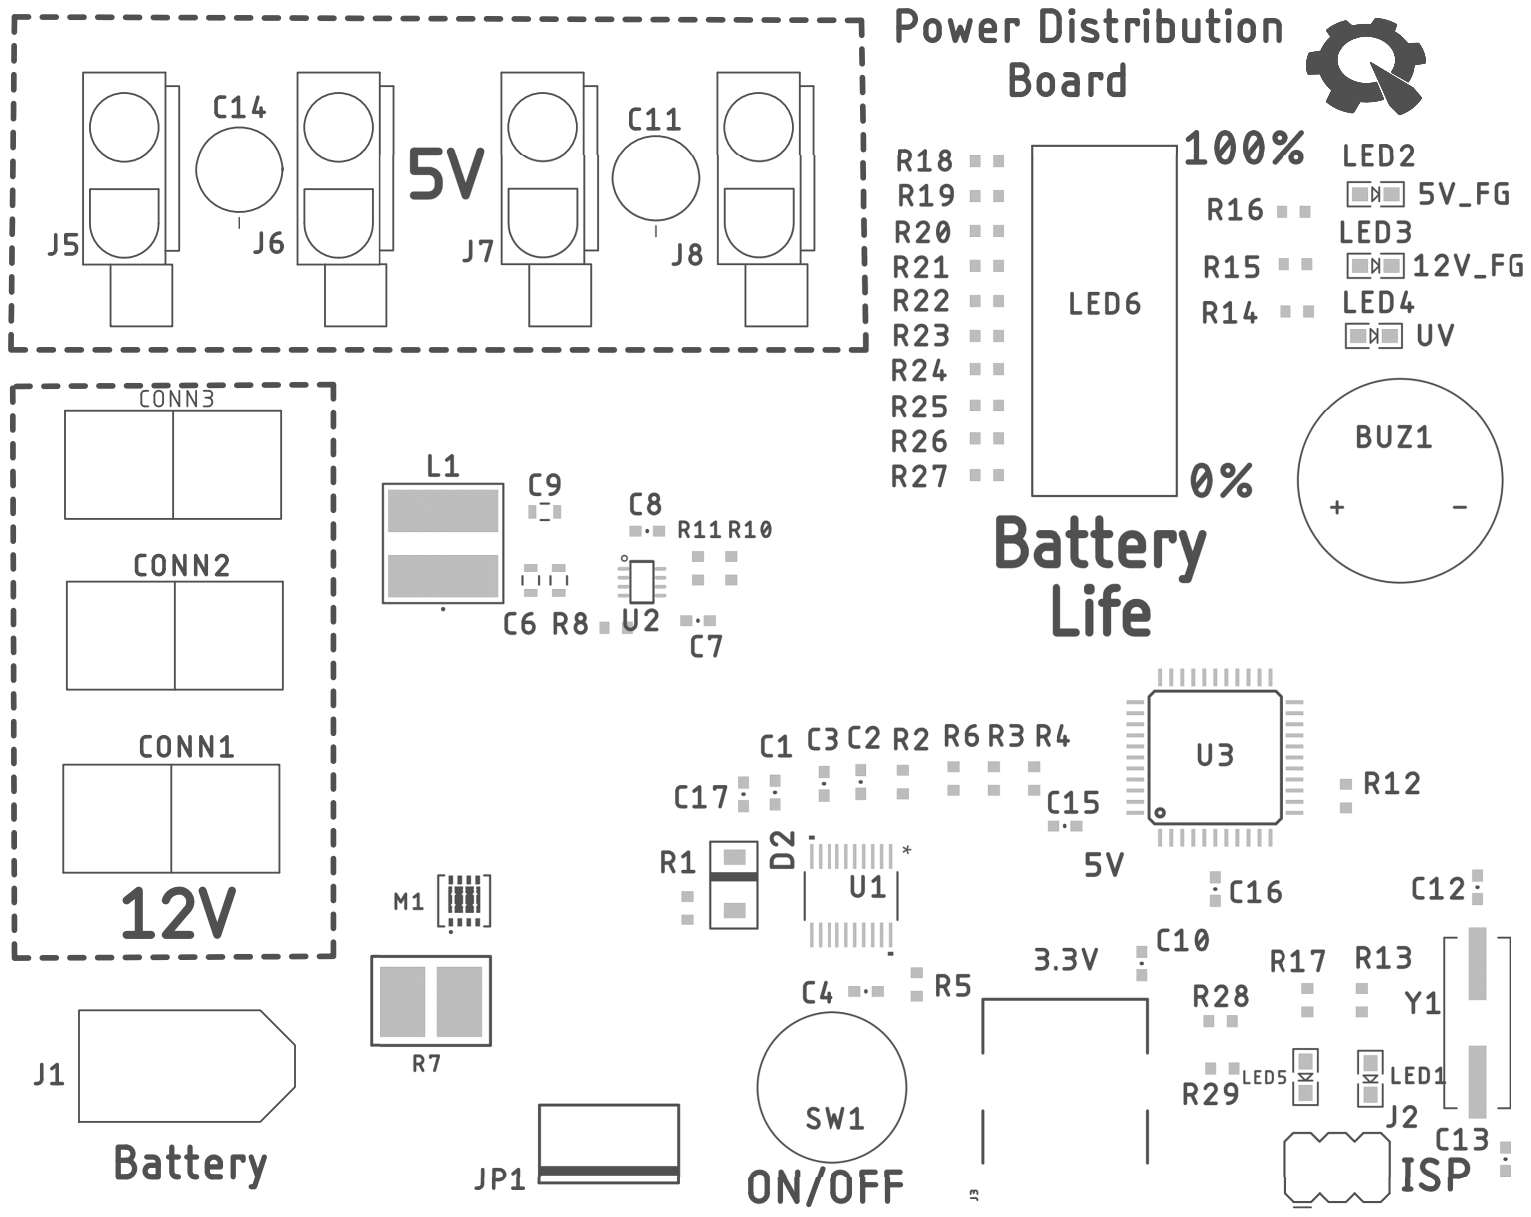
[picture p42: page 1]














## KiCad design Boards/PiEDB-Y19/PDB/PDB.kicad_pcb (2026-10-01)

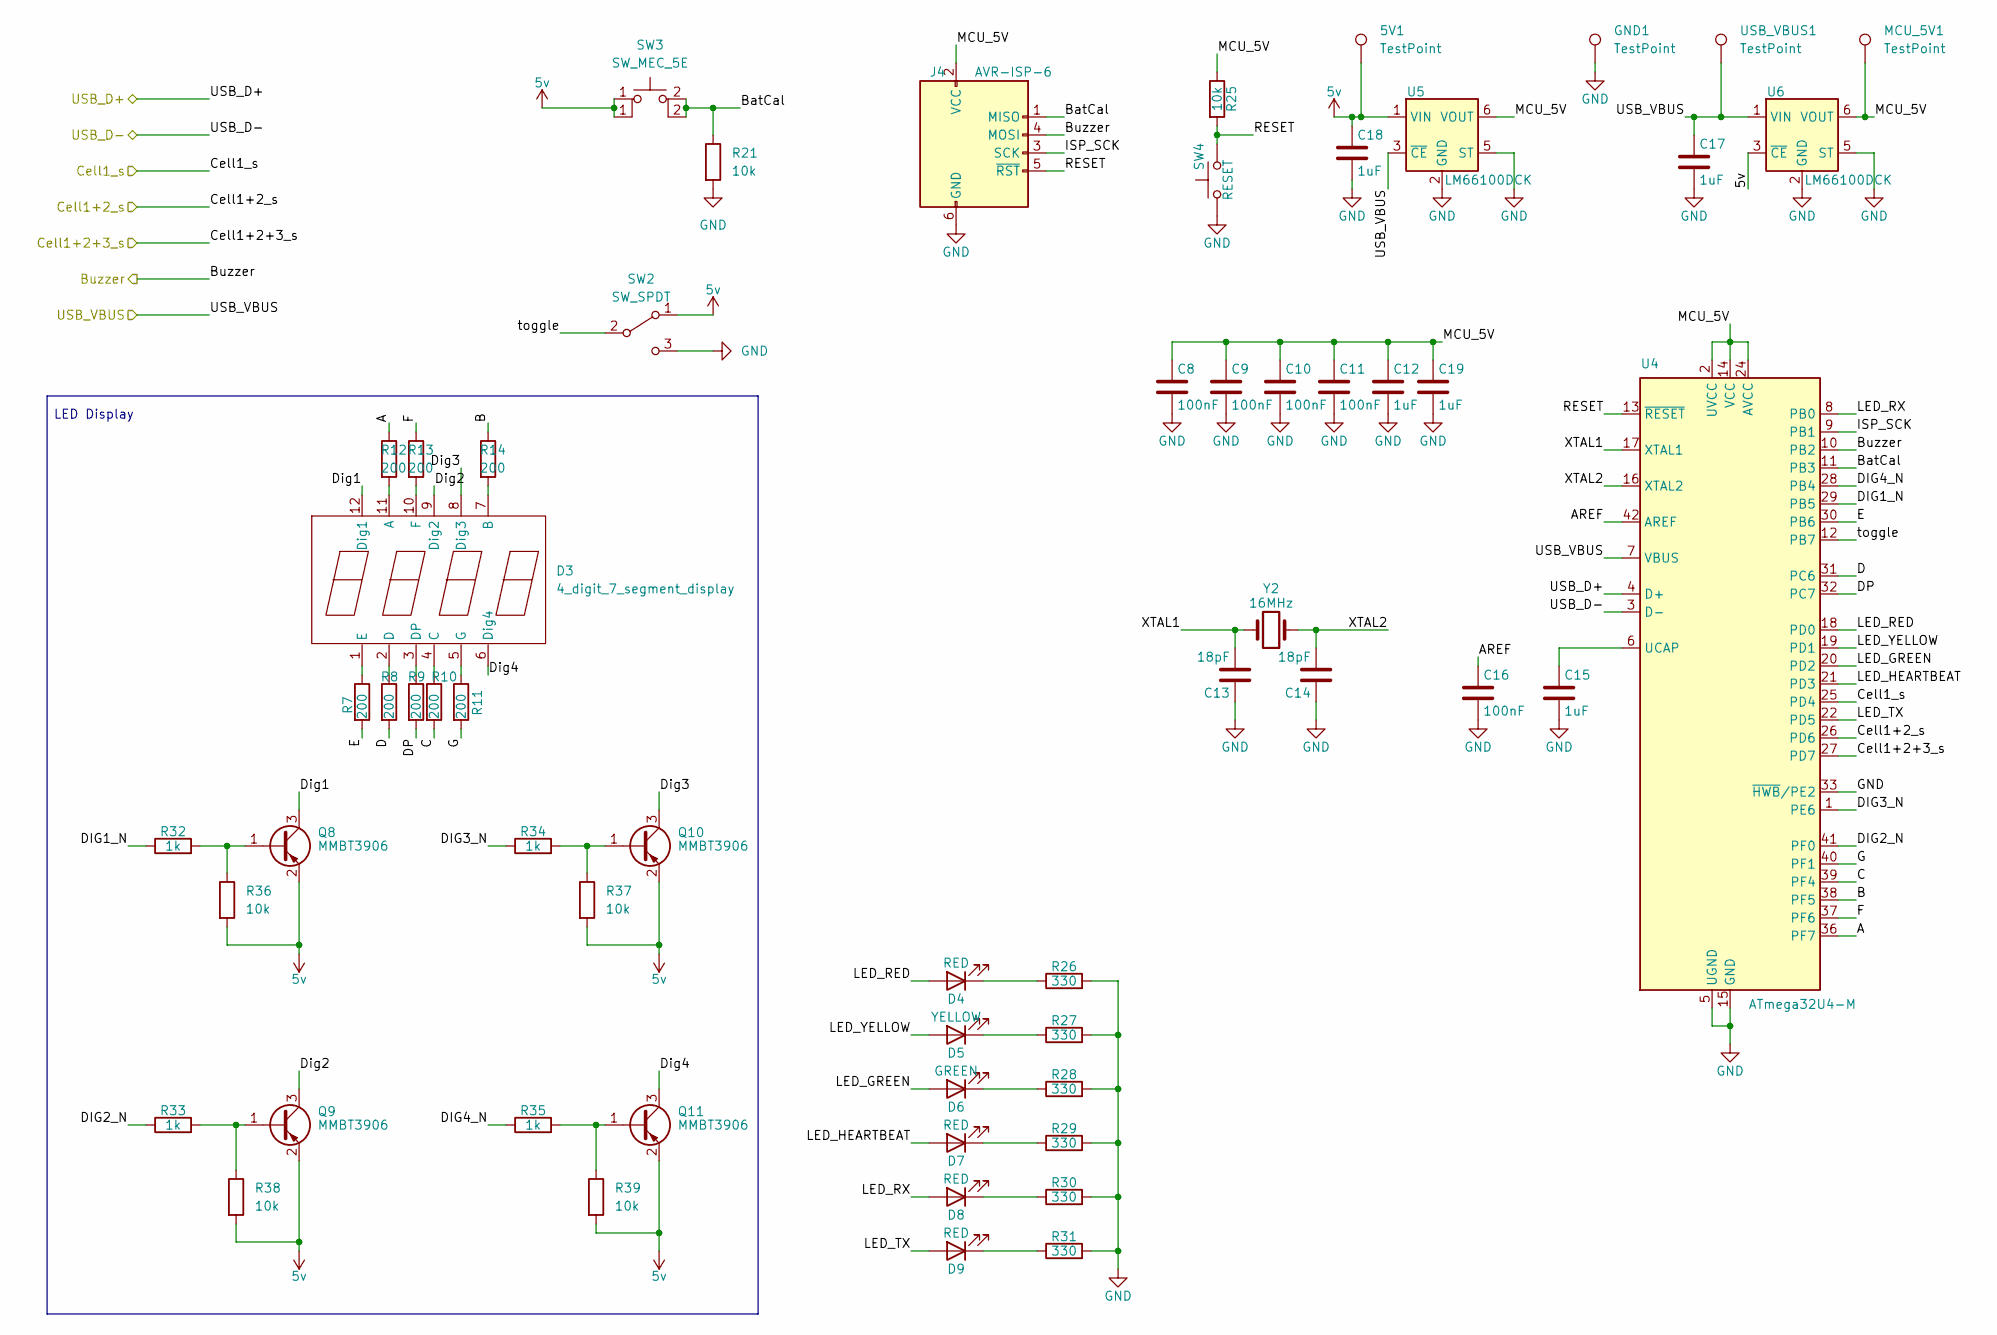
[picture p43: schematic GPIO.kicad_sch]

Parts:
5V1: TestPoint; TestPoint_Loop_D2.60mm_Drill0.9mm_Beaded
C8, C9, C10, C11, C16: 100nF; C_0603_1608Metric
C12, C15, C17, C18, C19: 1uF; C_0603_1608Metric
C13, C14: 18pF; C_0603_1608Metric
D3: 4_digit_7_segment_display; LED-SEG-TH_12P-L30.0-W13.7-P2.54-S10.16-BL
D4, D7, D8, D9: RED; LED_0805_2012Metric
D5: YELLOW; LED_0805_2012Metric
D6: GREEN; LED_0805_2012Metric
GND1: TestPoint; TestPoint_Loop_D2.60mm_Drill0.9mm_Beaded
J4: AVR-ISP-6; PinHeader_2x03_P2.54mm_Vertical
MCU_5V1: TestPoint; TestPoint_Loop_D2.60mm_Drill0.9mm_Beaded
Q8, Q9, Q10, Q11: MMBT3906; SOT-23
R7, R8, R9, R10, R11, R12, R13, R14: 200; R_0603_1608Metric
R21, R36, R37, R38, R39: 10k; R_0402_1005Metric
R25: 10k; R_0603_1608Metric
R26, R27, R28, R29, R30, R31: 330; R_0603_1608Metric
R32, R33, R34, R35: 1k; R_0603_1608Metric
SW2: SW_SPDT; DEALON SS-12D01-G3
SW3: SW_MEC_5E; SW_PUSH_6mm
SW4: RESET; SW_PUSH_6mm
U4: ATmega32U4-M; QFN-44-1EP_7x7mm_P0.5mm_EP5.2x5.2mm
U5, U6: LM66100DCK; SOT-363_SC-70-6
USB_VBUS1: TestPoint; TestPoint_Loop_D2.60mm_Drill0.9mm_Beaded
Y2: 16MHz; Crystal_SMD_5032-2Pin_5.0x3.2mm

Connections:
5v: 5V1.1 (1_1), C18.1, Q8.2 (E), Q9.2 (E), Q10.2 (E), Q11.2 (E), R36.2, R37.2, R38.2, R39.2, SW2.1 (A), SW3.1, U5.1 (VIN), U6.3 (~CE); also elsewhere on the board
/Buzzer: J4.4 (MOSI), U4.10 (PB2); also elsewhere on the board
/Cell1+2+3_s: U4.27 (PD7); also elsewhere on the board
/Cell1+2_s: U4.26 (PD6); also elsewhere on the board
/Cell1_s: U4.25 (PD4); also elsewhere on the board
/GPIO/A: R12.1, U4.36 (PF7)
/GPIO/AREF: C16.1, U4.42 (AREF)
/GPIO/B: R14.1, U4.38 (PF5)
/GPIO/BatCal: J4.1 (MISO), R21.1, SW3.2 (A), U4.11 (PB3)
/GPIO/C: R10.2, U4.39 (PF4)
/GPIO/D: R8.2, U4.31 (PC6)
/GPIO/DIG1_N: R32.1, U4.29 (PB5)
/GPIO/DIG2_N: R33.1, U4.41 (PF0)
/GPIO/DIG3_N: R34.1, U4.1 (PE6)
/GPIO/DIG4_N: R35.1, U4.28 (PB4)
/GPIO/DP: R9.2, U4.32 (PC7)
/GPIO/Dig1: D3.12 (Dig1), Q8.3 (C)
/GPIO/Dig2: D3.9 (Dig2), Q9.3 (C)
/GPIO/Dig3: D3.8 (Dig3), Q10.3 (C)
/GPIO/Dig4: D3.6 (Dig4), Q11.3 (C)
/GPIO/E: R7.2, U4.30 (PB6)
/GPIO/F: R13.1, U4.37 (PF6)
/GPIO/G: R11.2, U4.40 (PF1)
/GPIO/ISP_SCK: J4.3 (SCK), U4.9 (PB1)
/GPIO/LED_GREEN: D6.2 (A), U4.20 (PD2)
/GPIO/LED_HEARTBEAT: D7.2 (A), U4.21 (PD3)
/GPIO/LED_RED: D4.2 (A), U4.18 (PD0)
/GPIO/LED_RX: D8.2 (A), U4.8 (PB0)
/GPIO/LED_TX: D9.2 (A), U4.22 (PD5)
/GPIO/LED_YELLOW: D5.2 (A), U4.19 (PD1)
/GPIO/MCU_5V: C8.1, C9.1, C10.1, C11.1, C12.1, C19.1, J4.2 (VCC), MCU_5V1.1 (1_1), R25.1, U4.2 (UVCC), U4.14 (VCC), U4.24 (AVCC), U4.34 (VCC), U4.44 (AVCC), U5.6 (VOUT), U6.6 (VOUT)
/GPIO/RESET: J4.5 (~RST), R25.2, SW4.2, U4.13 (~RESET)
/GPIO/USB_D+: U4.4 (D+); also elsewhere on the board
/GPIO/USB_D-: U4.3 (D-); also elsewhere on the board
/GPIO/USB_VBUS: C17.1, U4.7 (VBUS), U5.3 (~CE), U6.1 (VIN), USB_VBUS1.1 (1_1); also elsewhere on the board
/GPIO/XTAL1: C13.2, U4.17 (XTAL1), Y2.2
/GPIO/XTAL2: C14.2, U4.16 (XTAL2), Y2.1
/GPIO/toggle: SW2.2 (B), U4.12 (PB7)
GND: C8.2, C9.2, C10.2, C11.2, C12.2, C13.1, C14.1, C15.2, C16.2, C17.2, C18.2, C19.2, GND1.1 (1_1), J4.6 (GND), R21.2, R26.2, R27.2, R28.2, R29.2, R30.2, R31.2, SW2.3 (C), SW4.1, U4.5 (UGND), U4.15 (GND), U4.23 (GND), U4.33 (~HWB/PE2), U4.35 (GND), U4.43 (GND), U4.45 (GND), U5.2 (GND), U5.5 (ST), U6.2 (GND), U6.5 (ST); also elsewhere on the board
unnamed: D3.11 (A), R12.2
unnamed: D3.7 (B), R14.2
unnamed: D3.4 (C), R10.1
unnamed: D3.2 (D), R8.1
unnamed: D3.3 (DP), R9.1
unnamed: D3.1 (E), R7.1
unnamed: D3.10 (F), R13.2
unnamed: D3.5 (G), R11.1
unnamed: D4.1 (K), R26.1
unnamed: D5.1 (K), R27.1
unnamed: D6.1 (K), R28.1
unnamed: D7.1 (K), R29.1
unnamed: D8.1 (K), R30.1
unnamed: D9.1 (K), R31.1
unnamed: Q8.1 (B), R32.2, R36.1
unnamed: Q9.1 (B), R33.2, R38.1
unnamed: Q10.1 (B), R34.2, R37.1
unnamed: Q11.1 (B), R35.2, R39.1
unnamed: C15.1, U4.6 (UCAP)

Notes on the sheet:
LED Display

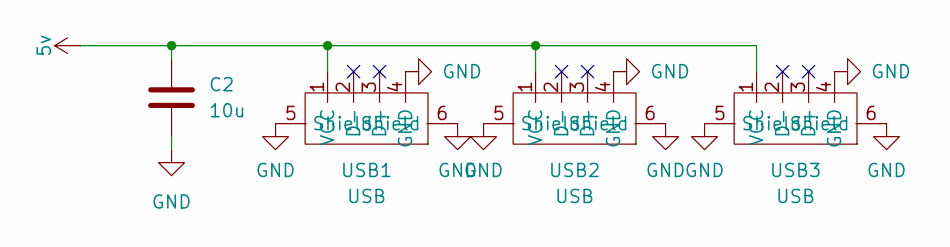
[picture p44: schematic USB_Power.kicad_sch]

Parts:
C2: 10u; CP_Radial_D5.0mm_P2.00mm
USB1, USB2, USB3: USB; USB-A_female

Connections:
5v: C2.1, USB1.1 (VCC), USB2.1 (VCC), USB3.1 (VCC); also elsewhere on the board
GND: C2.2, USB1.4 (GND), USB1.5 (Shield), USB1.6 (Shield), USB2.4 (GND), USB2.5 (Shield), USB2.6 (Shield), USB3.4 (GND), USB3.5 (Shield), USB3.6 (Shield); also elsewhere on the board

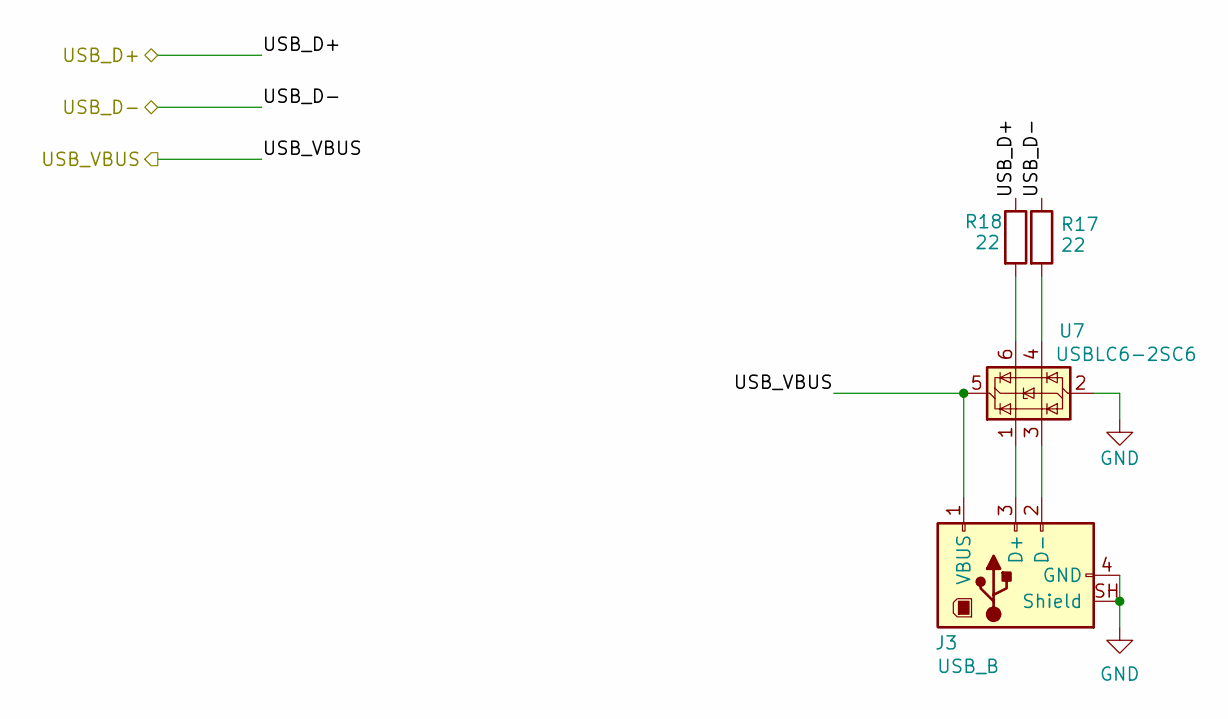
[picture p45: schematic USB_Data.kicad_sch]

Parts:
J3: USB_B; USB_B_OST_USB-B1HSxx_Horizontal
R17, R18: 22; R_0603_1608Metric
U7: USBLC6-2SC6; SOT-23-6

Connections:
/GPIO/USB_D+: R18.1; also elsewhere on the board
/GPIO/USB_D-: R17.1; also elsewhere on the board
/GPIO/USB_VBUS: J3.1 (VBUS), U7.5 (VBUS); also elsewhere on the board
GND: J3.4 (GND), J3.SH (Shield), U7.2 (GND); also elsewhere on the board
unnamed: J3.3 (D+), U7.1 (I/O1)
unnamed: J3.2 (D-), U7.3 (I/O2)
unnamed: R17.2, U7.4 (I/O2)
unnamed: R18.2, U7.6 (I/O1)

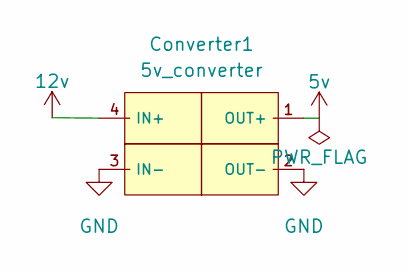
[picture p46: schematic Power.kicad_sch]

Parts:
Converter1: 5v_converter

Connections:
5v: Converter1.1 (OUT+); also elsewhere on the board
12v: Converter1.4 (IN+); also elsewhere on the board
GND: Converter1.2 (OUT-), Converter1.3 (IN-); also elsewhere on the board

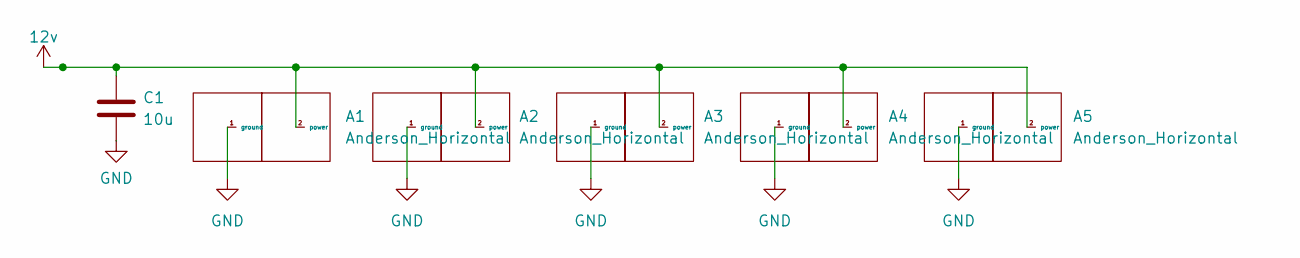
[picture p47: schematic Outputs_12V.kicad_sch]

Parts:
A1, A2, A3, A4, A5: Anderson_Horizontal; anderson_horizontal
C1: 10u; CP_Radial_D5.0mm_P2.00mm

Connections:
12v: A1.2 (power), A2.2 (power), A3.2 (power), A4.2 (power), A5.2 (power), C1.1; also elsewhere on the board
GND: A1.1 (ground), A2.1 (ground), A3.1 (ground), A4.1 (ground), A5.1 (ground), C1.2; also elsewhere on the board

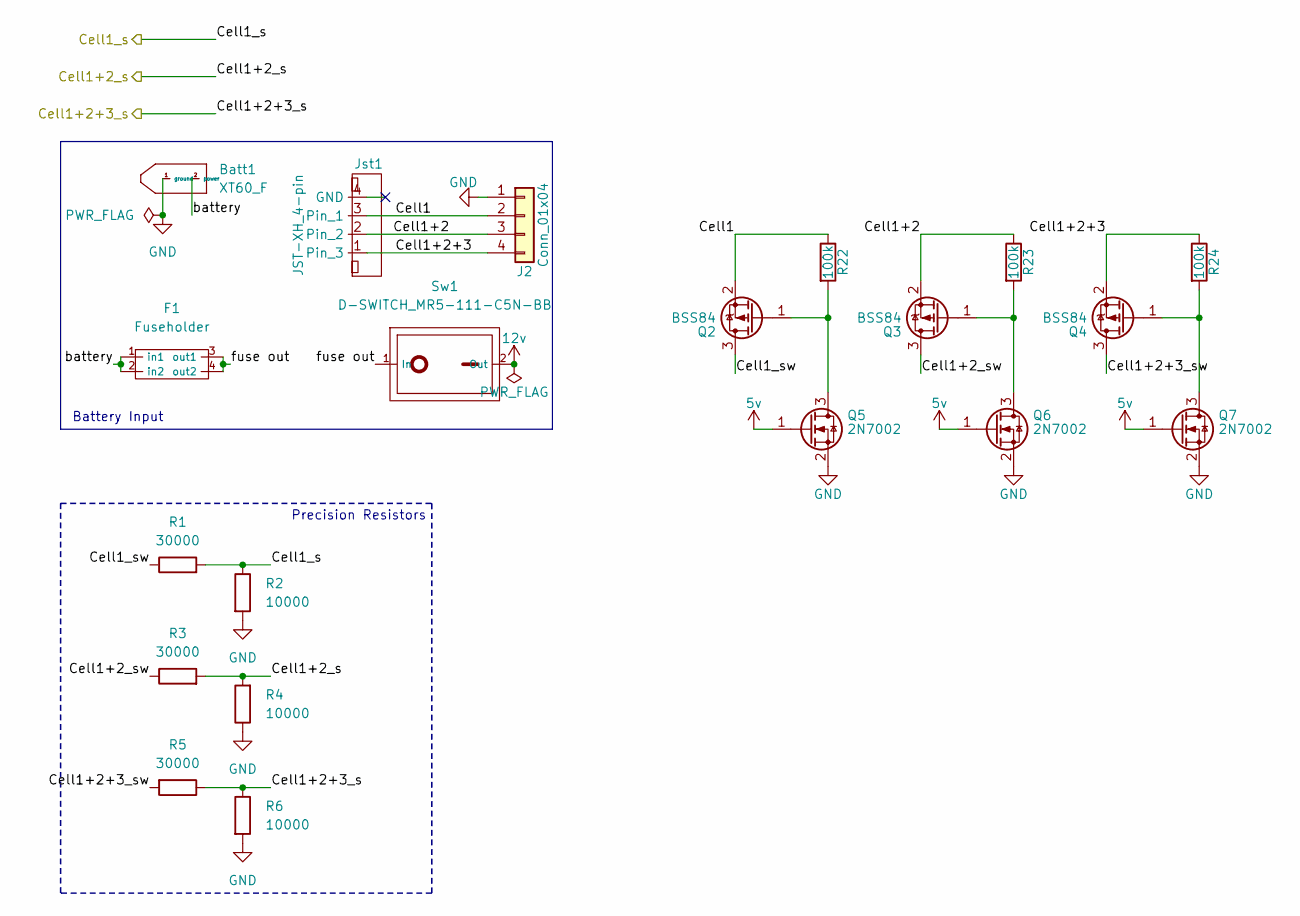
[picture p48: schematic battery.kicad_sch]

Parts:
Batt1: XT60_F; AMASS_XT60-M_1x02_P7.20mm_Vertical
F1: Fuseholder; Fuse Holder SMD
J2: Conn_01x04; PinHeader_1x04_P2.54mm_Vertical
Jst1: JST-XH_4-pin; JST_XH_B4B-XH-A_1x04_P2.50mm_Vertical
Q2, Q3, Q4: BSS84; SOT-23
Q5, Q6, Q7: 2N7002; SOT-23
R1, R3, R5: 30000; R_0603_1608Metric
R2, R4, R6: 10000; R_0603_1608Metric
R22, R23, R24: 100k; R_0603_1608Metric
Sw1: D-SWITCH_MR5-111-C5N-BB; Rocker Switch

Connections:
5v: Q5.1 (G), Q6.1 (G), Q7.1 (G); also elsewhere on the board
12v: Sw1.2 (Out); also elsewhere on the board
/Battery/Cell1: J2.2, Jst1.3 (Pin_1), Q2.2 (S), R22.1
/Battery/Cell1+2: J2.3, Jst1.2, Q3.2 (S), R23.1
/Battery/Cell1+2+3: J2.4, Jst1.1 (Pin_3), Q4.2 (S), R24.1
/Battery/Cell1+2+3_sw: Q4.3 (D), R5.2
/Battery/Cell1+2_sw: Q3.3 (D), R3.1
/Battery/Cell1_sw: Q2.3 (D), R1.1
/Battery/battery: Batt1.2 (power), F1.1 (in1), F1.2 (in2)
/Battery/fuse out: F1.3 (out1), F1.4 (out2), Sw1.1 (In)
/Cell1+2+3_s: R5.1, R6.1; also elsewhere on the board
/Cell1+2_s: R3.2, R4.2; also elsewhere on the board
/Cell1_s: R1.2, R2.1; also elsewhere on the board
GND: Batt1.1 (ground), J2.1, Q5.2 (S), Q6.2 (S), Q7.2 (S), R2.2, R4.1, R6.2; also elsewhere on the board
unnamed: Q2.1 (G), Q5.3 (D), R22.2
unnamed: Q3.1 (G), Q6.3 (D), R23.2
unnamed: Q4.1 (G), Q7.3 (D), R24.2

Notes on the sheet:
Precision Resistors
Battery Input

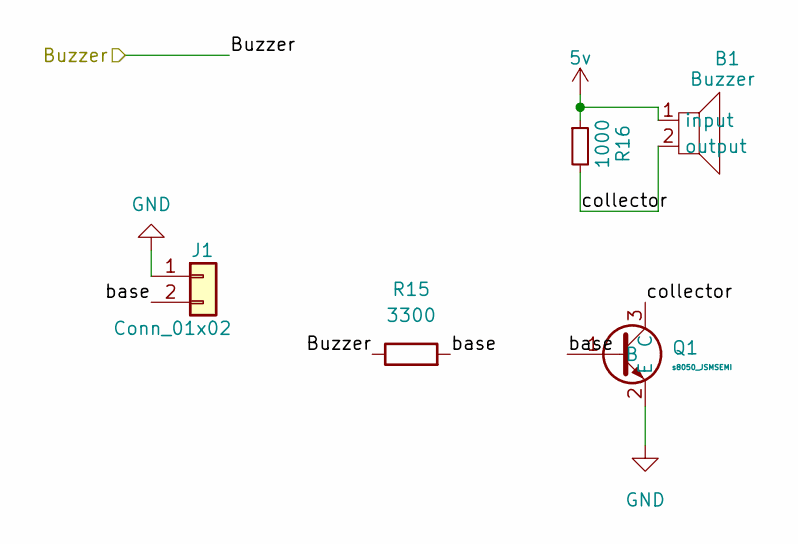
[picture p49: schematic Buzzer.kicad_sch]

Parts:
B1: Buzzer
J1: Conn_01x02; PinHeader_1x02_P2.54mm_Vertical
Q1: s8050_JSMSEMI; s8050 JSMSEMI
R15: 3300; R_0603_1608Metric
R16: 1000; R_0603_1608Metric

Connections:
5v: B1.1 (input), R16.1; also elsewhere on the board
/Buzzer: R15.1; also elsewhere on the board
/Buzzer/base: J1.2, Q1.1 (B), R15.2
/Buzzer/collector: B1.2 (output), Q1.3 (C), R16.2
GND: J1.1, Q1.2 (E); also elsewhere on the board

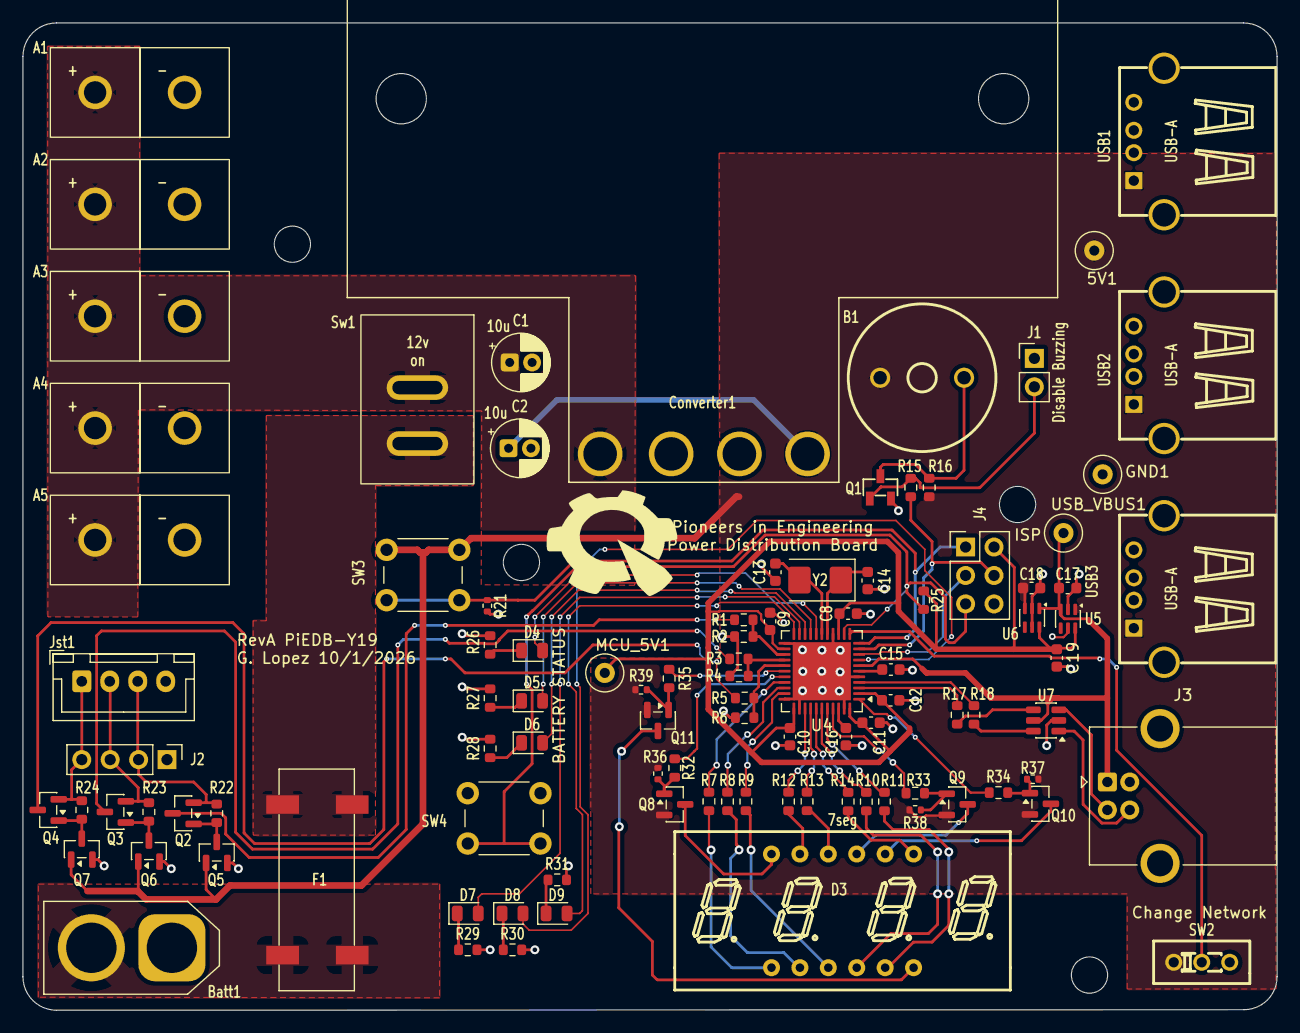
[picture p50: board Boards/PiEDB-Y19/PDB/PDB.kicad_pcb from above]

Board: 2 copper layers, 112.1 x 88.2 mm, 99 parts (0 on the bottom side), 76 nets.

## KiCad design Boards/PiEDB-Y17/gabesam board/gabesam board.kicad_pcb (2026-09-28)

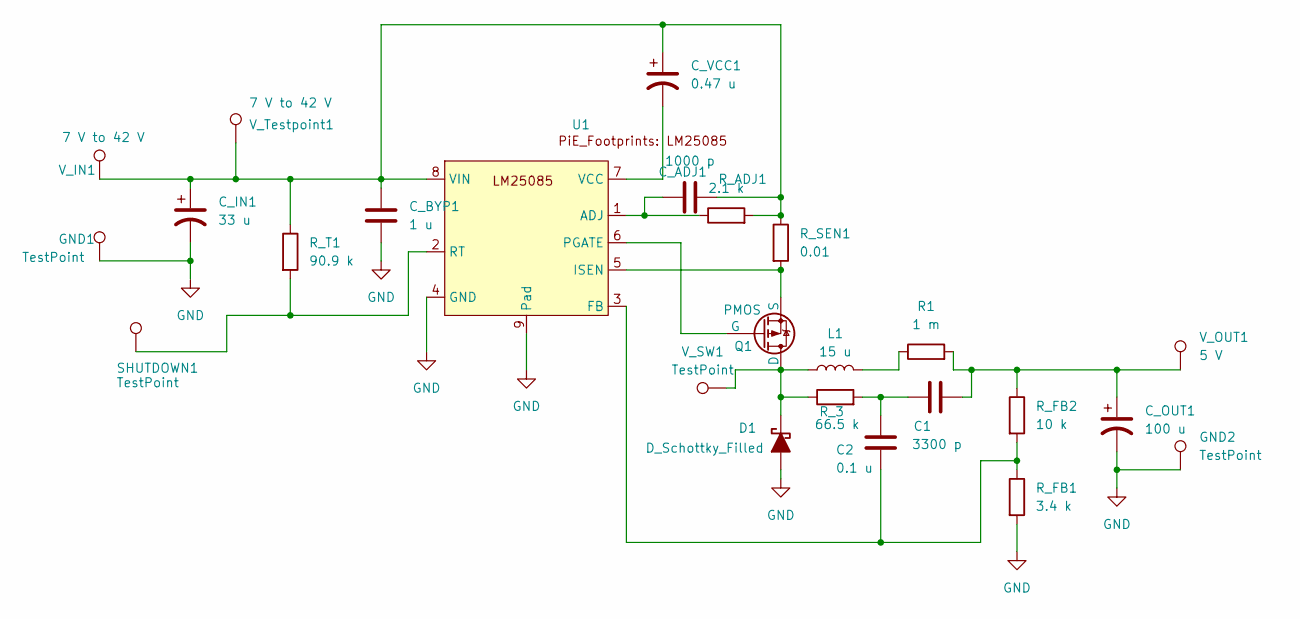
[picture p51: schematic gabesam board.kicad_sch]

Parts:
C1: 3300 p; C_1206
C2: 0.1 u; C_1206
C_ADJ1: 1000 p; C_1206
C_BYP1: 1 u; C_1206
C_IN1: 33 u; C_1206
C_OUT1: 100 u; C_1206
C_VCC1: 0.47 u; C_1206
D1: D_Schottky_Filled; D_1206_3216Metric_Pad1.42x1.75mm_HandSolder
GND1, GND2: TestPoint; TestPoint_Loop_D2.60mm_Drill0.9mm_Beaded
L1: 15 u; L_1206_3216Metric
Q1: PMOS; PowerPAK_SO-8_Single
R1: 1 m; R_1206
R_3: 66.5 k; R_1206
R_ADJ1: 2.1 k; R_1206
R_FB1: 3.4 k; R_1206
R_FB2: 10 k; R_1206
R_SEN1: 0.01; R_1206
R_T1: 90.9 k; R_1206
SHUTDOWN1: TestPoint; TestPoint_Loop_D2.60mm_Drill0.9mm_Beaded
U1: LM25085-Q1
V_IN1: 7 V to 42 V; TestPoint_Loop_D2.60mm_Drill0.9mm_Beaded
V_OUT1: 5 V; TestPoint_Loop_D2.60mm_Drill0.9mm_Beaded
V_SW1: TestPoint; TestPoint_Loop_D2.60mm_Drill0.9mm_Beaded
V_Testpoint1: 7 V to 42 V; TestPoint_Loop_D2.60mm_Drill0.9mm_Beaded

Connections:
GND: C_BYP1.2, C_IN1.2, C_OUT1.2, D1.2 (A), GND1.1, GND2.1, R_FB1.2, U1.4 (GND), U1.9 (Pad)
unnamed: C1.1, C2.2, R_3.2
unnamed: C1.2, C_OUT1.1, R1.2, R_FB2.1, V_OUT1.1
unnamed: D1.1 (K), L1.1, Q1.1 (D), R_3.1, V_SW1.1
unnamed: L1.2, R1.1
unnamed: Q1.2 (G), U1.6 (PGATE)
unnamed: Q1.3 (S), R_SEN1.2, U1.5 (ISEN)
unnamed: C_ADJ1.1, R_ADJ1.1, U1.1 (ADJ)
unnamed: C2.1, R_FB1.1, R_FB2.2, U1.3 (FB)
unnamed: R_T1.2, SHUTDOWN1.1, U1.2 (RT)
unnamed: C_VCC1.2, U1.7 (VCC)
unnamed: C_ADJ1.2, C_BYP1.1, C_IN1.1, C_VCC1.1, R_ADJ1.2, R_SEN1.1, R_T1.1, U1.8 (VIN), V_IN1.1, V_Testpoint1.1

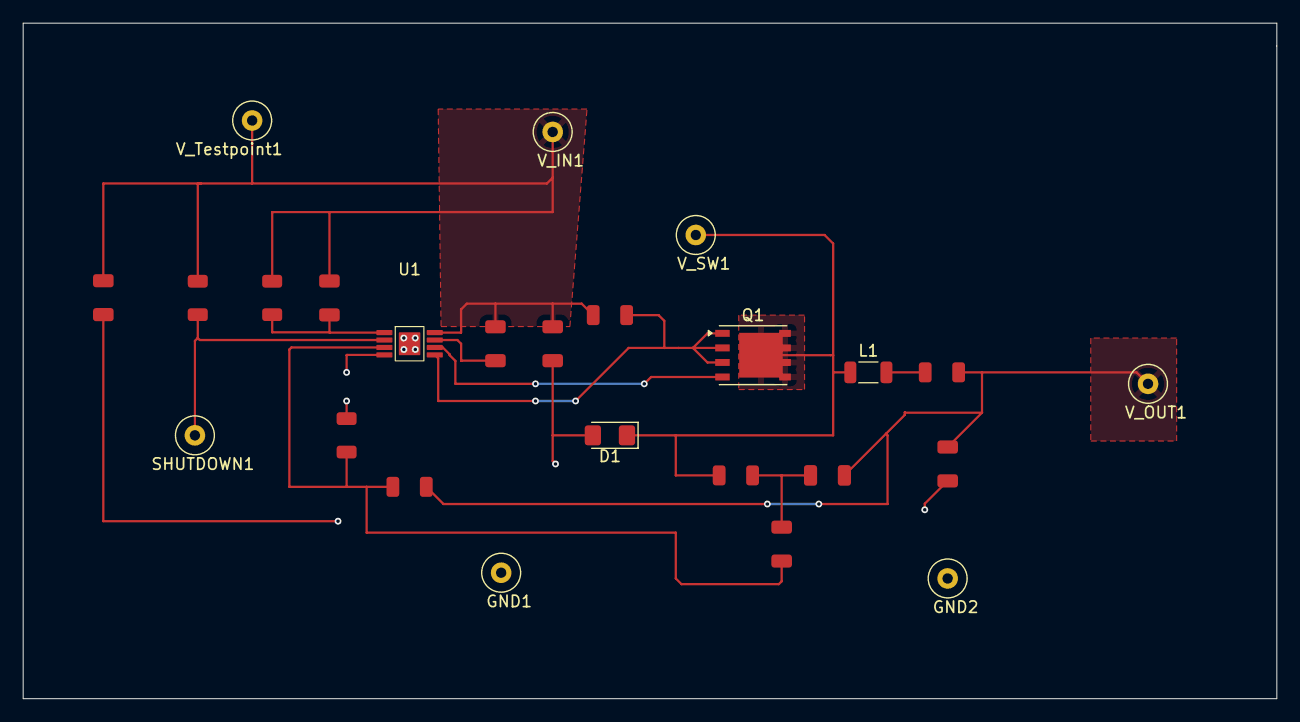
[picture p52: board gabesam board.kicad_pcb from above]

Board: 2 copper layers, 109.5 x 59.0 mm, 25 parts (0 on the bottom side), 12 nets.

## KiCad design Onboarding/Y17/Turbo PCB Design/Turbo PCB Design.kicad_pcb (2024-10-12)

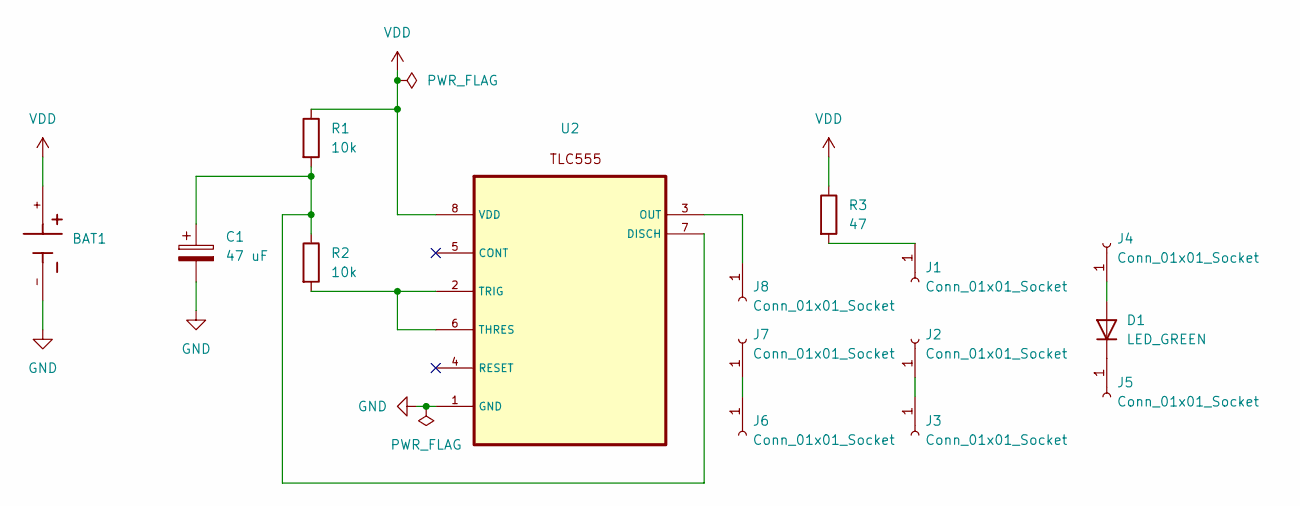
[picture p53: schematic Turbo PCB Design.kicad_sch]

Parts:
BAT1: BAT_BS-7
C1: 47 uF; CP_Radial_D4.0mm_P1.50mm
D1: LED_GREEN; LED_D5.0mm
J1, J2, J3, J4, J5, J6, J7, J8: Conn_01x01_Socket; MountingHole_1.0mm_M2_Pad
R1, R2: 10k; R_2512_6332Metric_Pad1.40x3.35mm_HandSolder
R3: 47; R_2512_6332Metric_Pad1.40x3.35mm_HandSolder
U2: TLC555_SCHE

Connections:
GND: BAT1.-, C1.2, U2.1 (GND)
unnamed: D1.2 (A), J4.1
unnamed: D1.1 (K), J5.1
unnamed: J1.1, R3.2
unnamed: J2.1, J3.1
unnamed: J6.1, J7.1
unnamed: J8.1, U2.3 (OUT)
unnamed: C1.1, R1.2, R2.1, U2.7 (DISCH)
unnamed: R2.2, U2.2 (TRIG), U2.6 (THRES)
VDD: BAT1.+, R1.1, R3.1, U2.8 (VDD)

Board: 2 copper layers, 15 parts (0 on the bottom side), 10 nets, no tracks yet.

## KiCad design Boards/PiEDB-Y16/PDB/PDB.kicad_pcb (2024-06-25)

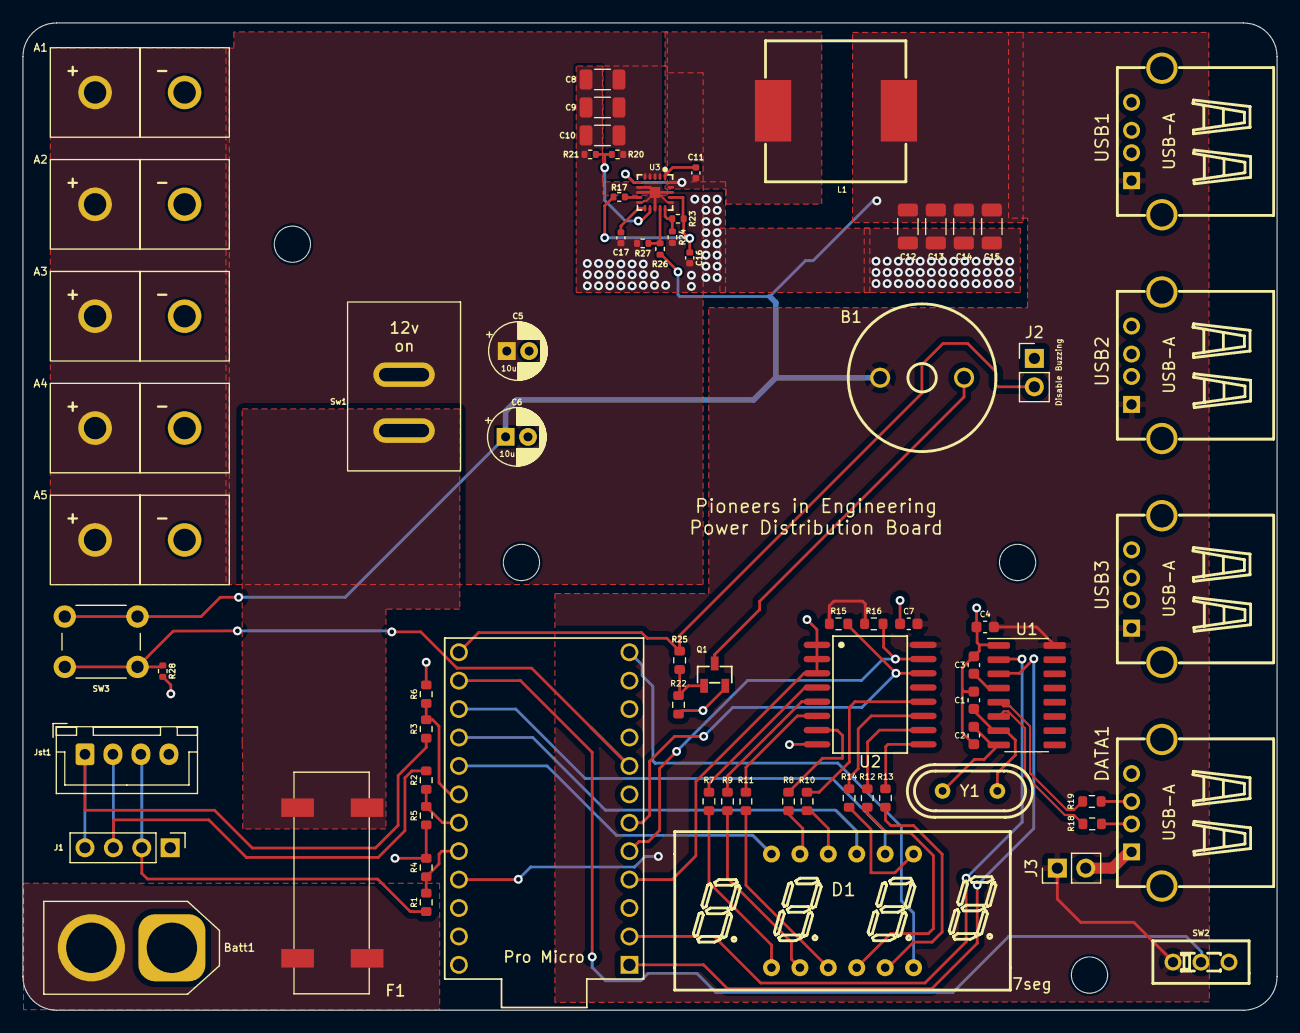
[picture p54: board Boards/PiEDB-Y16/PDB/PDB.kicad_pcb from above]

Board: 2 copper layers, 112.1 x 88.2 mm, 72 parts (0 on the bottom side), 56 nets.

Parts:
A1, A2, A3, A4, A5: Anderson_Horizontal; anderson_horizontal
B1: Buzzer
Batt1: XT60_F; AMASS_XT60-M_1x02_P7.20mm_Vertical
C1, C2: 22pF; C_0603_1608Metric
C3, C4: 0.1uF; C_0603_1608Metric
C5, C6: 10u; CP_Radial_D5.0mm_P2.00mm
C7: 0.1u; C_0603_1608Metric
C8, C9: 22u; C_1206_3216Metric
C10: 0.1u; C_1206_3216Metric
C11: 0.1u; C_0402_1005Metric
C12, C13, C14, C15: 47u; C_1206_3216Metric
C16, C17: 1u; C_0402_1005Metric
D1: 4_digit_7_segment_display; LED-SEG-TH_12P-L30.0-W13.7-P2.54-S10.16-BL
DATA1: USB; USB-A_female
F1: Fuseholder; Fuse Holder SMD
J1: Conn_01x04; PinHeader_1x04_P2.54mm_Vertical
J2, J3: Conn_01x02; PinHeader_1x02_P2.54mm_Vertical
Jst1: JST-XH_4-pin; JST_XH_B4B-XH-A_1x04_P2.50mm_Vertical
L1: 1.8u; 125CDMCCDS-1R8MC
Pro1: ProMicro; ProMicro-EnforcedTop
Q1: s8050_JSMSEMI; s8050 JSMSEMI
R1, R2, R3: 30000; R_0603_1608Metric
R4, R5, R6: 10000; R_0603_1608Metric
R7, R8, R9, R10, R11, R12, R13, R14: 200; R_0603_1608Metric
R15, R16: 4700; R_0603_1608Metric
R17, R20: 100k; R_0402_1005Metric
R18, R19: 22; R_0603_1608Metric
R21, R27: 15k; R_0402_1005Metric
R22: 2000; R_0603_1608Metric
R23: 200k; R_0402_1005Metric
R24: 33k; R_0402_1005Metric
R25: 100; R_0603_1608Metric
R26: 110k; R_0402_1005Metric
R28: 10k; R_0402_1005Metric
SW2: SW_SPDT; DEALON SS-12D01-G3
SW3: SW_MEC_5E; SW_PUSH_6mm
Sw1: D-SWITCH_MR5-111-C5N-BB; Rocker Switch
U1: CH340G; SOP-16_3.9x9.9mm_P1.27mm
U2: PCF8574; PCF8574T
U3: TPS56C230RJER
USB1, USB2, USB3: USB; USB-A_female
Y1: 12MHz; JYJE S1C12000VWFAC

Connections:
/5v: B1.1 (input), C4.1, C6.1, C7.2, C12.2, C13.2, C14.2, C15.2, J3.1, L1.2, Pro1.21 (VCC), R15.1, R16.1, R26.1, SW2.1 (A), SW3.1, SW3.2, U1.16 (VCC), U2.16 (VDD), USB1.1 (VCC), USB2.1 (VCC), USB3.1 (VCC)
/12v: A1.2 (power), A2.2 (power), A3.2 (power), A4.2 (power), A5.2 (power), C5.1, C8.2, C9.2, C10.2, R20.1, Sw1.2 (Out), U3.2 (VIN), U3.3 (VIN), U3.4 (VIN), U3.5 (VIN)
/A: R8.1, U2.7 (P3)
/B: R14.1, U2.11 (P6)
/BST: C11.2, U3.1 (BST)
/BatCal: Pro1.8 (5), R28.1, SW3.3 (K), SW3.4 (A)
/Buzzer: J2.2, Pro1.13 (10), R25.2
/C: R12.2, U2.10 (P5)
/Cell1: J1.2, Jst1.3 (Pin_1), R1.1
/Cell1+2: J1.3, Jst1.2, R2.1
/Cell1+2+3: J1.4, Jst1.1 (Pin_3), R3.2
/Cell1+2+3_s: Pro1.18 (A1), R3.1, R6.1
/Cell1+2_s: Pro1.19 (A2), R2.2, R5.2
/Cell1_s: Pro1.20 (A3), R1.2, R4.1
/D: R9.2, U2.5 (P1)
/D+: R19.1, U1.5 (UD+)
/D-: R18.1, U1.6 (UD-)
/DP: R11.2, U2.6 (P2)
/Dig1: D1.12 (Dig1), Pro1.17 (A0)
/Dig2: D1.9 (Dig2), Pro1.16 (15)
/Dig3: D1.8 (Dig3), Pro1.15 (14)
/Dig4: D1.6 (Dig4), Pro1.12 (9)
/E: R7.2, U2.4 (P0)
/EN: R20.2, R21.1, U3.12 (EN)
/F: R10.1, U2.12 (P7)
/FB: R26.2, R27.1, U3.14 (FB)
/G: R13.2, U2.9 (P4)
/MODE: R23.2, R24.1, U3.15 (MODE)
/Rx: Pro1.2 (RX), U1.2 (TXD)
/SCL: Pro1.6 (3), R15.2, U2.14 (SCL)
/SDA: Pro1.5 (2), R16.2, U2.15 (SDA)
/SW: C11.1, L1.1, U3.6 (SW), U3.19 (SW), U3.20 (SW)
/Tx: Pro1.1 (TX), U1.3 (RXD)
/VCC: C16.1, R17.1, R23.1, U3.17 (VCC)
/battery: Batt1.2 (power), F1.1 (in1), F1.2 (in2)
/collector: B1.2 (output), Q1.3 (C)
/fuse out: F1.3 (out1), F1.4 (out2), Sw1.1 (In)
/toggle: Pro1.14 (16), SW2.2 (B)
GND: A1.1 (ground), A2.1 (ground), A3.1 (ground), A4.1 (ground), A5.1 (ground), Batt1.1 (ground), C1.2, C2.2, C3.2, C4.2, C5.2, C6.2, C7.1, C8.1, C9.1, C10.1, C12.1, C13.1, C14.1, C15.1, C16.2, C17.2, DATA1.4 (GND), DATA1.5 (Shield), DATA1.6 (Shield), J1.1, J2.1, Pro1.3 (GND), Pro1.4 (GND), Pro1.23 (GND), Q1.2 (E), R4.2, R5.1, R6.2, R21.2, R22.1, R24.2, R27.2, R28.2, SW2.3 (C), U1.1 (GND), U2.1 (A0), U2.2 (A1), U2.3 (A2), U2.8 (VSS), U3.7 (PGND), U3.8 (PGND), U3.10 (NC), U3.13 (AGND), U3.16 (NC), U3.18 (PGND), U3.21 (PGND), USB1.4 (GND), USB1.5 (Shield), USB1.6 (Shield), USB2.4 (GND), USB2.5 (Shield), USB2.6 (Shield), USB3.4 (GND), USB3.5 (Shield), USB3.6 (Shield)
unnamed: D1.11 (A), R8.2
unnamed: D1.7 (B), R14.2
unnamed: D1.4 (C), R12.1
unnamed: D1.2 (D), R9.1
unnamed: D1.3 (DP), R11.1
unnamed: D1.1 (E), R7.1
unnamed: D1.10 (F), R10.2
unnamed: D1.5 (G), R13.1
unnamed: DATA1.3 (D+), R19.2
unnamed: DATA1.2 (D-), R18.2
unnamed: DATA1.1 (VCC), J3.2
unnamed: Q1.1 (B), R22.2, R25.1
unnamed: C3.1, U1.4 (V3)
unnamed: C1.1, U1.7 (XI), Y1.1
unnamed: C2.1, U1.8 (XO), Y1.2
unnamed: R17.2, U3.9 (PGOOD)
unnamed: C17.1, U3.11 (SS)

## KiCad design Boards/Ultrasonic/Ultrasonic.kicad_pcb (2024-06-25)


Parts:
R1: 2k; R_0603_1608Metric_Pad0.98x0.95mm_HandSolder
R2: 1k; R_0603_1608Metric_Pad0.98x0.95mm_HandSolder
U1: ProMicro
U2: HC-SR04; XCVR_HC-SR04

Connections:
GND: R1.1, U1.3 (GND), U1.4 (GND), U1.23 (GND), U2.4 (GND)
unnamed: R1.2, R2.1, U1.14 (B2)
unnamed: R2.2, U2.3 (ECHO)
unnamed: U1.15 (B3), U2.2 (TRIG)
unnamed: U1.21 (VCC), U2.1 (VCC)


Board: 2 copper layers, 40.5 x 45.8 mm, 4 parts (0 on the bottom side), 5 nets.

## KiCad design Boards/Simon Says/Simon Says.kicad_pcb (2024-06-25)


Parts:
D1, D2, D3, D4, D5: LED; LED_D5.0mm_FlatTop
LS1: Speaker; BUZZER_PS1440P02BT
R1, R4: 220; R_0805_2012Metric_Pad1.20x1.40mm_HandSolder
R2, R3: 100; R_0805_2012Metric_Pad1.20x1.40mm_HandSolder
R5: 160; R_0805_2012Metric_Pad1.20x1.40mm_HandSolder
SW1, SW2, SW3, SW4: SW_PUSH; SW_PUSH_6mm
TP1, TP2: TestPoint; TestPoint_Pad_1.0x1.0mm
U1: ProMicro

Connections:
/B: R3.2, U1.18 (F6)
/G: R2.2, U1.19 (F5)
/R: R1.1, U1.20 (F4)
/SW1: D1.2 (A), SW1.2, U1.16 (B1)
/SW2: D2.2 (A), SW2.2, U1.15 (B3)
/SW3: D3.2 (A), SW3.2, U1.14 (B2)
/SW4: D4.2 (A), SW4.2, U1.13 (B6)
/Y: R4.2, U1.17 (F7)
GND: R5.2, SW1.1, SW2.1, SW3.1, SW4.1, TP1.1, U1.3 (GND), U1.4 (GND), U1.23 (GND)
unnamed: D1.1 (K), R1.2
unnamed: D2.1 (K), R2.1
unnamed: D3.1 (K), R3.1
unnamed: D4.1 (K), R4.1
unnamed: D5.1 (K), R5.1
unnamed: LS1.1, U1.12 (B5)
unnamed: LS1.2, U1.11 (B4)
VCC: D5.2 (A), TP2.1, U1.21 (VCC)

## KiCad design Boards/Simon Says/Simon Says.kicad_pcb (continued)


Board: 2 copper layers, 104.4 x 58.1 mm, 18 parts (0 on the bottom side), 17 nets.

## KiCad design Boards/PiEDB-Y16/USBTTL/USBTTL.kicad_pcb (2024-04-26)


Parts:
C1: 0.01uF; C_0603_1608Metric
C2: 0.1uF; C_0603_1608Metric
C3, C4: 22pF; C_0603_1608Metric
J1, J2: Conn_01x08_Pin; PinHeader_1x08_P2.54mm_Vertical
R1, R2: 22; R_0603_1608Metric
U1: CH340G; SOIC-16_3.9x9.9mm_P1.27mm
USB1: USB_Type_A; USB-A_female
Y1: 12MHz; JYJE S1C12000VWFAC

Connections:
/CTS: J2.8, U1.9 (~CTS)
/D+: J1.4, R2.2, U1.5 (UD+)
/D-: J1.3, R1.2, U1.6 (UD-)
/DCD: J2.5, U1.12 (~DCD)
/DSR: J2.7, U1.10 (~DSR)
/DTR: J2.4, U1.13 (~DTR)
/Data+: R2.1, USB1.3 (D+)
/Data-: R1.1, USB1.2 (D-)
/R232: J2.2, U1.15 (R232)
/RI: J2.6, U1.11 (~RI)
/RTS: J2.3, U1.14 (~RTS)
/Rx: J1.6, U1.3 (RXD)
/Tx: J1.7, U1.2 (TXD)
/V3: C1.1, J1.5, U1.4 (V3)
/VCC: C2.1, J2.1, U1.16 (VCC), USB1.1 (VCC)
/Xi: C3.1, J1.2, U1.7 (XI), Y1.1
/Xo: C4.1, J1.1, U1.8 (XO), Y1.2
GND: C1.2, C2.2, C3.2, C4.2, J1.8, U1.1 (GND), USB1.4 (GND), USB1.5 (Shield), USB1.6 (Shield)


Board: 2 copper layers, 26.0 x 32.0 mm, 11 parts (0 on the bottom side), 18 nets.

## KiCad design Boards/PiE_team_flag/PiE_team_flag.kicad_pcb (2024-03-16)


Board: 2 copper layers, 45.7 x 50.8 mm, 7 parts (0 on the bottom side), 6 nets.

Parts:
C1: .1uF; C_0603_1608Metric
J1: USB_B; OST_USB-B1HSB6
LED1: YEL; LED_D5.0mm
LED2: BLU; LED_D5.0mm
R1: 145; R_0603_1608Metric
R2: 90; R_0603_1608Metric
SW1: SW_SP3T; XKB Connectivity SS13D75L3

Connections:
GND: C1.1, J1.4 (GND), J1.P1, J1.P2, LED1.1 (K), LED2.1 (K)
unnamed: C1.2, J1.1 (VBUS), SW1.3
unnamed: LED1.2 (A), R1.1
unnamed: LED2.2 (A), R2.1
unnamed: R1.2, SW1.1
unnamed: R2.2, SW1.4

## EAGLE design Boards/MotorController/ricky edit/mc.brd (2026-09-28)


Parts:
C1, C3: 0.1 µF; 0603-CAP
C2, C4: 47 µF; 1206
C5, C6: 18pF; 0603-CAP
C7: 1 uF; 0603-CAP
C8: 1uF; 0603-CAP
C9, C10, C11, C12: 0.1 uF; 0402-CAP
C13, C14: LELON_ELECTROLYTIC_CAP; LELON_CAP
CONN1, CONN2, CONN3: ANDERSONVERTICAL; ANDERSON_VERTICAL
ENC1, ENC2: M041X04-MTA; 1X04-MTA
J1: USB_B_PTH; USB-B-PTH
J2: AVR_SPI_PRG_6MA03-2; MA03-2
LED1, LED4, LED5: RED; LED-0805
LED2: YELLOW; LED-0805
LED3: GREEN; LED-0805
MC1, MC2: DRV8872DDAR; DDA0008H_N_TEX
R1, R2, R3: 10k; R0603
R4: 330; 4X-0603
R5: 10k; 4X-0603
R6, R7: 22; R0603
R8: 330; R0603
U1: ATMEGA32U4-MU; QFN50P700X700X100-45N
Y1: CRYSTAL; CRYSTAL-SMD-5.0X3.2-2PIN

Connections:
A1: ENC1.3, R5.4, U1.21 ((TXD1/INT3)PD3)
A2: ENC1.4, R5.3, U1.36 (PF7(ADC7/TDI))
AIN1: MC1.3 (IN1), U1.31 (PC6(OC3A/!OC4A!))
AIN2: MC1.2 (IN2), U1.29 (PB5(PCINT5/OC1A/!OC4B!/ADC))
AOUT1: CONN2.PIN2 (OUTA), MC1.6 (OUT1)
AOUT2: CONN2.PIN1 (OUTB), MC1.8 (OUT2)
B1: ENC2.3, R5.2, U1.19 ((SDA/INT1)PD1)
B2: ENC2.4, R5.1, U1.20 ((RXD1/INT2)PD2)
BIN1: MC2.3 (IN1), U1.27 (PD7(T0/OC4D/ADC10))
BIN2: MC2.2 (IN2), U1.18 ((OC0B/SCL/INT0)PD0)
BOUT1: CONN3.PIN2 (OUTA), MC2.6 (OUT1)
BOUT2: CONN3.PIN1 (OUTB), MC2.8 (OUT2)
D+: J1.D+, R7.1
D-: J1.D-, R6.1
FAULT_N: MC1.4 (FAULT_N), MC2.4 (FAULT_N), R1.2, R2.2, U1.22 ((XCK1/!CTS!)PD5)
GND: C1.2, C2.2, C3.2, C4.2, C5.2, C6.2, C7.1, C8.2, C9.1, C10.1, C11.1, C12.1, C13.P$2 (-), C14.P$2 (-), CONN1.PIN1 (OUTB), ENC1.1, ENC2.1, J1.GND, J1.SHLD1 (SHLD), J1.SHLD2 (SHLD), J2.6, MC1.1 (GND), MC1.7 (ISEN), MC1.9 (PAD), MC1.P$1 (PAD), MC1.P$2 (PAD), MC1.P$3 (PAD), MC1.P$4 (PAD), MC1.P$5 (PAD), MC1.P$6 (PAD), MC2.1 (GND), MC2.7 (ISEN), MC2.9 (PAD), MC2.P$1 (PAD), MC2.P$2 (PAD), MC2.P$3 (PAD), MC2.P$4 (PAD), MC2.P$5 (PAD), MC2.P$6 (PAD), R4.1, R4.2, R4.3, R4.4, R8.2, U1.5 (UGND), U1.15 (GND), U1.23 (GND), U1.33 (PE2(!HWB!)), U1.35 (GND), U1.43 (GND)
HEARTBEAT: LED5.A, U1.38 (PF5(ADC5/TMS))
LED1: LED1.A, U1.39 (PF4(ADC4/TCK))
LED2: LED2.A, U1.40 (PF1(ADC1))
LED3: LED3.A, U1.41 (PF0(ADC0))
LR1: LED1.C, R4.8
LR2: LED2.C, R4.7
LR3: LED3.C, R4.6
LR4: LED4.C, R4.5
unnamed: C6.1, U1.17 (XTAL1), Y1.P$2 (2)
unnamed: R7.2, U1.4 (D+)
unnamed: R6.2, U1.3 (D-)
unnamed: C8.1, U1.6 (UCAP)
unnamed: C5.1, U1.16 (XTAL2), Y1.P$1 (1)
unnamed: LED5.C, R8.1
RST: J2.5, R3.1, U1.13 (!RESET!)
RXLED: LED4.A, U1.8 ((SS/PCINT0)PB0)
SCLK: J2.3, U1.9 ((PCINT1/SCLK)PB1)
SDATI: J2.4, U1.10 ((PDI/PCINT2/MOSI)PB2)
SDATO: J2.1, U1.11 ((PDO/PCINT3/MISO)PB3)
VCC: C7.2, C9.2, C10.2, C11.2, C12.2, ENC1.2, ENC2.2, J1.VBUS, J2.2, R1.1, R2.1, R3.2, R5.5, R5.6, R5.7, R5.8, U1.2 (UVCC), U1.7 (VBUS), U1.14 (VCC), U1.24 (AVCC), U1.34 (VCC), U1.42 (AREF), U1.44 (AVCC)
VM: C1.1, C2.1, C3.1, C4.1, C13.P$1 (+), C14.P$1 (+), CONN1.PIN2 (OUTA), MC1.5 (VM), MC2.5 (VM)


Board: 2 copper layers, 67.0 x 72.0 mm, 42 parts (0 on the bottom side), 37 nets.

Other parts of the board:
U$1, U$2, U$4: STAND-OFF
U$5: PIE-LOGO

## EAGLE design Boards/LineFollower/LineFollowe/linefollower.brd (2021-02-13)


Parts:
C1: 10mF; 0402-CAP
C2: 1mF; 0402-CAP
C3: 10nF; 0402-CAP
C4: 100nF; 0402-CAP
C5: 0.1uF; 0402-CAP
IC1: ARDUINO_PRO_MICRO
LED1: RED; LED-0603
Q1, Q2, Q3, Q4, Q5, Q6: QRE1113; DIP4_100AQ_ONS
R1, R3: 1k; R0603
R2, R4: 10k; R0603
R5: 330; R0603
RF1, RF2: 1K; R0603
R_GND: 100K; R0603
R_LED1, R_LED2, R_LED3, R_LED4, R_LED5, R_LED6: 100; R0603
R_VCC: 100K; R0603
U1: AD8630ARUZ-REEL; RU_14_ADI
U4: 74VHC153FT(BJ); TSSOP16B_TOS

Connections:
CTRL_A: IC1.14, U4.14
CTRL_B: IC1.16, U4.2
DIFF_1+: R3.2, R4.2, U1.10 (+INC)
DIFF_1-: R1.2, R2.2, U1.9 (-INC)
GND: C1.2, C2.2, C3.2, C4.2, C5.1, IC1.GND@0 (GND), IC1.GND@1 (GND), IC1.GND@2 (GND), LED1.C, Q1.2, Q1.4, Q2.2, Q2.4, Q3.2, Q3.4, Q4.2, Q4.4, Q5.2, Q5.4, Q6.2, Q6.4, R_GND.1, U1.3 (+INA), U1.5 (+INB), U1.11 (V-), U4.3, U4.8, U4.13
IR_LED_1: IC1.A3, R_LED1.2, R_LED2.2
IR_LED_2: IC1.A2, R_LED3.2, R_LED4.2
IR_LED_3: IC1.15, R_LED5.2, R_LED6.2
unnamed: Q2.1, R_LED2.1
unnamed: LED1.A, R5.1
unnamed: Q1.1, R_LED1.1
unnamed: Q3.1, R_LED3.1
unnamed: Q4.1, R_LED4.1
unnamed: Q5.1, R_LED5.1
unnamed: Q6.1, R_LED6.1
SENS_1: IC1.A1, R2.1, R5.2, U1.8 (OUTC)
STROBE_1: IC1.A0, U4.1
STROBE_2: IC1.10, U4.15
TIA_1: Q1.3, U4.6
TIA_2: Q2.3, U4.10
TIA_3: Q3.3, U4.5
TIA_4: Q4.3, U4.11
TIA_5: Q5.3, U4.4
TIA_6: Q6.3, U4.12
TIA_A: RF1.1, U1.2 (-INA), U4.7
TIA_B: RF2.2, U1.6 (-INB), U4.9
VCC: C1.1, C2.1, C3.1, C4.1, IC1.VCC, R_VCC.2, U1.4 (V+), U4.16
VIR_GND: C5.2, R4.1, R_GND.2, R_VCC.1
VO1_1: R1.1, RF1.2, U1.1 (OUTA)
VO2_1: R3.1, RF2.1, U1.7 (OUTB)

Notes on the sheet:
virtual ground to center diff amp around 2.5
decoupling caps
photosensor output feedback
diff amp (gain = R2/R1 = 10)
TIAs (gain = RF = 1000)
trigger IR LED


Board: 2 copper layers, 120.0 x 52.0 mm, 30 parts (0 on the bottom side), 30 nets.

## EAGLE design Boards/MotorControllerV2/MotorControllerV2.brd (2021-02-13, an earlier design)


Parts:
C1, C4: 1uF; 0603-CAP
C5, C6: 18pF; 0603-CAP
ENC1, ENC2: M041X04-MTA; 1X04-MTA
J1: AVR_SPI_PRG_6MA03-2; MA03-2
J2: USB_B_PTH; USB-B-PTH
LED1, LED4, LED5: RED; LED-1206
LED2: YELLOW; LED-1206
LED3: GREEN; LED-1206
R1: 10k; R0603
R2, R3: 22; R0603
R4: 330; 4X-0603
R8: 10k; 4X-0603
R9: 330; R0603
U2: ATMEGA32U4-AU; TQFP44
Y1: CRYSTAL10.5X4.8; CRYSTAL-SMD-10.5X4.8-2PIN

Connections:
A1: ENC1.3, R8.8, U2.21 ((TXD1/INT3)PD3)
A2: ENC1.4, R8.7, U2.36 ((ADC7/TDI)PF7)
AIN1: U2.31 ((OC3A/OC4A)PC6); also elsewhere on the board
AIN2: U2.29 ((PCINT5/OC1A/OC4B/ADC12)PB5); also elsewhere on the board
B1: ENC2.3, R8.6, U2.19 ((SDA/INT1)PD1)
B2: ENC2.4, R8.5, U2.20 ((RXD1/INT2)PD2)
BIN1: U2.27 ((T0/OC4D/ADC10)PD7); also elsewhere on the board
BIN2: U2.18 ((OSC0B/SCL/INT0)PD0); also elsewhere on the board
D+: J2.D+, R3.1
D-: J2.D-, R2.1
FAULTN: U2.22 ((XCK1/CTS)PD5); also elsewhere on the board
GND: C1.1, C4.1, C5.1, C6.1, ENC1.1, ENC2.1, J1.6, J2.GND, J2.SHLD1 (SHIELD), J2.SHLD2 (SHIELD), R4.1, R4.2, R4.3, R4.4, R9.2, U2.5 (UGND), U2.15 (GND), U2.23 (GND2), U2.33 ((HWB)PE2), U2.35 (GND3), U2.43 (GND4); also elsewhere on the board
HEARTBEAT: LED5.A, U2.38 ((ADC5/TMS)PF5)
LED1: LED1.A, U2.39 ((ADC4/TCK)PF4)
LED2: LED2.A, U2.40 ((ADC1)PF1)
LED3: LED3.A, U2.41 ((ADC0)PF0)
unnamed: R2.2, U2.3 (D-)
unnamed: R3.2, U2.4 (D+)
unnamed: LED4.C, R4.8
unnamed: LED1.C, R4.5
unnamed: LED2.C, R4.6
unnamed: LED3.C, R4.7
unnamed: C6.2, U2.17 (XTAL1), Y1.P$2 (2)
unnamed: C5.2, U2.16 (XTAL2), Y1.P$1 (1)
unnamed: LED5.C, R9.1
unnamed: C1.2, U2.6 (UCAP)
RESET: U2.30 ((PCINT6/OC1B/OC4B/ADC13)PB6); also elsewhere on the board
RST: J1.5, R1.1, U2.13 (RESET)
RXLED: LED4.A, U2.8 ((SS/PCINT0)PB0)
SCLK: J1.3, U2.9 ((PCINT1/SCLK)PB1); also elsewhere on the board
SCS: U2.12 ((PCINT7/OC0A/OC1C/RTS)PB7); also elsewhere on the board
SDATI: J1.4, U2.10 ((PDI/PCINT2/MOSI)PB2); also elsewhere on the board
SDATO: J1.1, U2.11 ((PDO/PCINT3/MISO)PB3); also elsewhere on the board
SLEEP: U2.32 ((ICP3/CLK0/OC4A)PC7); also elsewhere on the board
VCC: C4.2, ENC1.2, ENC2.2, J1.2, J2.VBUS, R1.2, R8.1, R8.2, R8.3, R8.4, U2.2 (UVCC), U2.7 (VBUS), U2.14 (VCC), U2.24 (AVCC), U2.34 (VCC2), U2.42 (AREF), U2.44 (AVCC2)


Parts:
C18, C21: 1uF; 0603-CAP
C19, C20, C22, C25, C28: .1uF; 0603-CAP
C23, C24, C26, C27: 220uF; NIPPON_F80
CONN1, CONN2, CONN3: ANDERSONVERTICAL; ANDERSON_VERTICAL
M1, M2, M3, M4, M5, M6, M7, M8: NMOS_CSD17579Q3A; DNH0008A
R5: 10k; R0603
R6, R7: 10m; R2512
U3: DRV8704; HTSSOP(38)

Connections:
A1HS: M1.4 (G), U3.P36 (A1HS)
A1LS: M2.4 (G), U3.P35 (AILS)
A2HS: M3.4 (G), U3.P31 (A2HS)
A2LS: M4.4 (G), U3.P32 (A2LS)
AIN1: U3.P10 (AIN1); also elsewhere on the board
AIN2: U3.P11 (AIN2); also elsewhere on the board
AISENP: M2.1 (S), M2.2 (S), M2.3 (S), M4.1 (S), M4.2 (S), M4.3 (S), R6.2, U3.P34 (AISENP)
AOUT1: CONN2.PIN1 (OUTB), M1.1 (S), M1.2 (S), M1.3 (S), M2.5 (D), M2.6 (D), M2.7 (D), M2.8 (D), M2.9 (D), U3.P37 (AOUT1)
AOUT2: CONN2.PIN2 (OUTA), M3.1 (S), M3.2 (S), M3.3 (S), M4.5 (D), M4.6 (D), M4.7 (D), M4.8 (D), M4.9 (D), U3.P30 (AOUT2)
B1HS: M5.4 (G), U3.P27 (B1HS)
B1LS: M6.4 (G), U3.P26 (B1LS)
B2HS: M7.4 (G), U3.P22 (B2HS)
B2LS: M8.4 (G), U3.P23 (B2LS)
BIN1: U3.P12 (BIN1); also elsewhere on the board
BIN2: U3.P13 (BIN2); also elsewhere on the board
BISENP: M6.1 (S), M6.2 (S), M6.3 (S), M8.1 (S), M8.2 (S), M8.3 (S), R7.2, U3.P25 (BISENP)
BOUT1: CONN1.PIN1 (OUTB), M5.1 (S), M5.2 (S), M5.3 (S), M6.5 (D), M6.6 (D), M6.7 (D), M6.8 (D), M6.9 (D), U3.P28 (BOUT1)
BOUT2: CONN1.PIN2 (OUTA), M7.1 (S), M7.2 (S), M7.3 (S), M8.5 (D), M8.6 (D), M8.7 (D), M8.8 (D), M8.9 (D), U3.P21 (BOUT2)
CP1: C22.2, U3.P1 (CP1)
CP2: C22.1, U3.P2 (CP2)
FAULTN: R5.2, U3.P18 (FAULTN); also elsewhere on the board
GND: C18.1, C19.1, C20.1, C23.-, C24.-, C25.1, C26.-, C27.-, C28.1, CONN3.PIN2 (OUTA), R6.1, R7.1, U3.P5 (GND), U3.P19 (GND2), U3.P24 (BISENN), U3.P29 (GND3), U3.P33 (AISENN), U3.P38 (GND4), U3.P39 (GND_PAD), U3.P40 (GND_PAD), U3.P41 (GND_PAD), U3.P42 (GND_PAD), U3.P43 (GND_PAD), U3.P44 (GND_PAD), U3.P45 (GND_PAD), U3.P46 (GND_PAD), U3.P47 (GND_PAD), U3.P48 (GND_PAD), U3.P49 (GND_PAD), U3.P50 (GND_PAD), U3.P51 (GND_PAD); also elsewhere on the board
RESET: U3.P9 (RESET); also elsewhere on the board
SCLK: U3.P14 (SCLK); also elsewhere on the board
SCS: U3.P16 (SCS); also elsewhere on the board
SDATI: U3.P15 (SDATI); also elsewhere on the board
SDATO: U3.P17 (SDATO); also elsewhere on the board
SLEEP: U3.P8 (SLEEPN); also elsewhere on the board
V5: C19.2, R5.1, U3.P6 (V5)
VCP: C21.1, U3.P3 (VCP)
VINT: C18.2, U3.P7 (VINT)
VPWR: C20.2, C21.2, C23.+, C24.+, C25.2, C26.+, C27.+, C28.2, CONN3.PIN1 (OUTB), M1.5 (D), M1.6 (D), M1.7 (D), M1.8 (D), M1.9 (D), M3.5 (D), M3.6 (D), M3.7 (D), M3.8 (D), M3.9 (D), M5.5 (D), M5.6 (D), M5.7 (D), M5.8 (D), M5.9 (D), M7.5 (D), M7.6 (D), M7.7 (D), M7.8 (D), M7.9 (D), U3.P4 (VM)


Board: 2 copper layers, 79.2 x 70.2 mm, 53 parts (1 on the bottom side), 55 nets.

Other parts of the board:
U$1: PIE-LOGO-SMALL
U$2: OSHW-LOGO-M
U$3, U$4, U$5, U$6: STAND-OFF

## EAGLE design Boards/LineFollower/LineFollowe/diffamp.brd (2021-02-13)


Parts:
C1: 10mF; 0402-CAP
C2: 1mF; 0402-CAP
C3: 10nF; 0402-CAP
C4: 100nF; 0402-CAP
Q1: QRE1113; DIP4_100AQ_ONS
R1, R2: 1k; R0603
R3, R4: 2000; R0603
R5: 10k; R0603
RDIODE: 100; R0603
RF1, RF2: 2000; R0603
RTEST: 100; R0603
U1: AD8630ARUZ-REEL; RU_14_ADI
U$1: 12PIN

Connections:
+INC: R2.2, R4.2, U1.10 (+INC)
-INA: Q1.3, R5.2, RF1.2, U1.2 (-INA)
-INB: RF2.1, RTEST.1, U1.6 (-INB)
-INC: R1.2, R3.2, U1.9 (-INC)
GND: C1.2, C2.2, C3.2, C4.2, Q1.2, Q1.4, U1.11 (V-), U$1.P$7
unnamed: RDIODE.2, U$1.P$8
unnamed: Q1.1, RDIODE.1
unnamed: RTEST.2, U$1.P$10
VCC: C1.1, C2.1, C3.1, C4.1, R5.1, U1.4 (V+), U$1.P$11
VCM0: U1.3 (+INA), U$1.P$9
VCM1: U1.5 (+INB), U$1.P$6
VCM2: R4.1, U$1.P$5
VO1: R2.1, RF1.1, U1.1 (OUTA), U$1.P$4
VO2: R1.1, RF2.2, U1.7 (OUTB), U$1.P$3
VOUT: R3.1, U1.8 (OUTC), U$1.P$12

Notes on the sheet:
Not sure if we need to pull the phototransitor high or if the TIA will bias it


Board: 2 copper layers, 41.9 x 52.1 mm, 16 parts (0 on the bottom side), 15 nets.

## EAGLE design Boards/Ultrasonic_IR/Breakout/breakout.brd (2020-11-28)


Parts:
IC1: ARDUINO_PRO_MICRO
J_ULTRASONIC_1: HC-SR04; HC-SR04_FOOTPRINT
LED1: Red; LED-0603
LED2: Green; LED-0603
LED3: Yellow; LED-0603
R2, R4, R5: 330R; R0603
U$1: IR; 1X03

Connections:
ECHO: IC1.14, J_ULTRASONIC_1.ECHO
GND: IC1.GND@0 (GND), IC1.GND@1 (GND), IC1.GND@2 (GND), J_ULTRASONIC_1.GND, R2.1, R4.1, R5.1, U$1.2 (GND)
unnamed: LED1.C, R5.2
unnamed: IC1.6, LED1.A
unnamed: IC1.5, LED3.A
unnamed: IC1.4, LED2.A
unnamed: LED2.C, R2.2
unnamed: LED3.C, R4.2
OUT: IC1.10, U$1.3 (OUT)
TRIG: IC1.16, J_ULTRASONIC_1.TRIG
VCC: IC1.VCC, J_ULTRASONIC_1.VCC (5V), U$1.1 (VCC)


Board: 2 copper layers, 58.0 x 34.0 mm, 9 parts (0 on the bottom side), 11 nets.

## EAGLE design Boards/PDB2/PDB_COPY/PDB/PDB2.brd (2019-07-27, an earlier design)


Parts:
BUT1: D6C90F1LFS; D6C_BUTTON
C1, C3: 2.2uF; 0603-CAP
C2: 1uF; 0603-CAP
C4: .1uF; 0603-CAP
D1: 220mV; SOD-323
J1: XT60CONNECTOR
J2: M041X04-MTA; 1X04-MTA
J3, J4: ANDERSONVERTICAL; ANDERSON_VERTICAL
J5, J6, J7, J8: ATX
M1, M2: STD20NF06LDPAK-M; DPAK-M
R1, R2: 3.3k; R0603
R3, R5: 10k; R0603
R6: 5.6k; R0603
R7: 499k; R0603
R8: 5m; SMD_SHUNT; MANUFACTURER_PART_NO WSHM28185L000FEA
U1: BQ7692006PWRPW20-M; PW20-M

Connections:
3.3V: C3.2, R1.2, R2.2, U1.8 (REGOUT); also elsewhere on the board
5V: J5.P$1, J6.P$1, J7.P$1, J8.P$1; also elsewhere on the board
12V: D1.1 (A), J1.12V, J3.PIN1 (OUTB), J4.PIN2 (OUTA), R5.2; also elsewhere on the board
ALERT: R7.1, U1.20 (ALERT); also elsewhere on the board
BCELL1: BUT1.U1.1, BUT1.U1.2, J2.2, U1.16 (VC1)
BCELL2: J2.3, U1.13 (VC4), U1.14 (VC3), U1.15 (VC2)
BCELL3: J2.4, U1.12 (VC5)
BOOT: BUT1.U2.1, BUT1.U2.2, R3.2, U1.6 (TS1); also elsewhere on the board
CAP1: C2.2, U1.7 (CAP1)
DSG: M1.1, M2.1, R6.2, U1.1 (DSG)
GND: C1.1, C2.1, C3.1, C4.2, J1.GND, J2.1, R3.1, R6.1, R7.2, R8.P$1 (1), U1.3 (VSS), U1.17 (VC0), U1.19 (SRN); also elsewhere on the board
GND_OUT: J3.PIN2 (OUTA), J4.PIN1 (OUTB), J5.P$2, J6.P$2, J7.P$2, J8.P$2, M1.3 (2), M2.3 (2); also elsewhere on the board
SCL: R2.1, U1.5 (SCL); also elsewhere on the board
SDA: R1.1, U1.4 (SDA); also elsewhere on the board
SRP: C4.1, M1.2 (3), M2.2 (3), R8.P$2 (2), U1.18 (SRP)
VIN: C1.2, D1.2 (C), R5.1, U1.9 (REGSRC), U1.10 (BAT)

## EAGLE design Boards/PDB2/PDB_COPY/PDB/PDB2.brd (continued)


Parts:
C5: 10uF; 0805
C6: .1uF; 0603-CAP
C7: 1000pF; 0603-CAP
C8: 22uF; 0805
L1: 2.2uH; ASPI
R20: 100k; R0603
U2: Value; RGT0016C

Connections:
5V: C8.2, L1.P$2 (2), R20.2, U2.7 (FSW), U2.14 (VOS); also elsewhere on the board
12V: C5.2, C6.2, U2.10 (AVIN), U2.11 (PVIN_2), U2.12 (PVIN), U2.13 (EN); also elsewhere on the board
GND_OUT: C5.1, C6.1, C7.1, C8.1, U2.5 (FB), U2.6 (AGND), U2.8 (DEF), U2.15 (PGND_2), U2.16 (PGND), U2.17 (EP); also elsewhere on the board
unnamed: L1.P$1 (1), U2.1 (SW_2), U2.2 (SW_3), U2.3 (SW)
unnamed: C7.2, U2.9 (SS_TR)
PG: R20.1, U2.4 (PG); also elsewhere on the board


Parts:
C9, C10: 18pF; 0603-CAP
C11: 1uF; 0603-CAP
J9: M03PTH; 1X03
J10: AVR_SPI_PROG_5X2LOCK; 2X5-SHROUDED_LOCK
J11: CONN_05X2NO_SILK; 2X5_NOSILK
J12: CONN_02; 1X02
LED1: BAR_SEGMENT_DISPLAY
R9: 10k; R0603
R10, R11, R12, R13, R14, R15, R16, R17, R18, R19: 220; R0603
U3: ATMEGA328PB-AU; TQFP32-08
Y1: ECX-53BSMDCRYSTAL; SMD_CRYSTAL

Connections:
3.3V: J9.3; also elsewhere on the board
5V_PROG: J9.1, J10.2 (VCC)
ALERT: J11.8; also elsewhere on the board
BOOT: J11.6; also elsewhere on the board
BOOT_IN: J11.5, U3.1 ((OC2B/INT1/PTCXY)PD3)
GND: C9.2, C10.2, C11.2, J10.4 (GND), J10.6 (GND), J10.8 (GND), J10.10 (GND), J11.9, J11.10, LED1.BAR_DISPLAY10 (P11), LED1.BAR_DISPLAY11 (P12), LED1.BAR_DISPLAY12 (P13), LED1.BAR_DISPLAY13 (P14), LED1.BAR_DISPLAY14 (P15), LED1.BAR_DISPLAY15 (P16), LED1.BAR_DISPLAY16 (P17), LED1.BAR_DISPLAY17 (P18), LED1.BAR_DISPLAY18 (P19), LED1.BAR_DISPLAY19 (P20), U3.5 (GND1), U3.21 (GND2), Y1.P1 (GND), Y1.P3 (GND); also elsewhere on the board
LED1: R10.1, U3.9 ((OC0B/T1/PTCXY)PD5)
LED2: R11.1, U3.10 ((OC0A/PTCXY/AIN0)PD6)
LED3: R12.1, U3.11 ((PTCXY/AIN1)PD7)
LED4: R13.1, U3.12 ((ICP1/CLKO/PTCXY)PB0)
LED5: R14.1, U3.13 (OC1A/PTCXY)PB1)
LED6: R15.1, U3.14 ((SS0/OC1B/PTCXY)PB2)
LED7: R16.1, U3.22 (PE3(ADC7/PTCY/T3/MOSI1))
LED8: R17.1, U3.23 (PC0(ADC0/PTCY/MISO1))
LED9: R18.1, U3.24 (PC1(ADC1/PTCY/SCK1))
LED10: R19.1, U3.25 (PC2(ADC2/PTCY))
MISO: J10.9 (MISO), U3.16 ((MISO0/RXD1/PTCXY)PB4)
MOSI: J10.1 (MOSI), U3.15 (MOSI0/TXD1/OC2A/PTCXY)PB3)
unnamed: J11.1, U3.27 (PC4(ADC4/PTCY/SDA0))
unnamed: C9.1, U3.7 ((XTAL1/TOSC1)PB6), Y1.P2 (2)
unnamed: C10.1, U3.8 ((XTAL2/TOSC2)PB7), Y1.P0 (1)
unnamed: J11.3, U3.28 (PC5(ADC5/PTCY/SCL0))
unnamed: J11.7, U3.32 (PD2(PTCXY/INT0/OC3B/OC4B))
unnamed: LED1.BAR_DISPLAY0 (P1), R10.2
unnamed: LED1.BAR_DISPLAY1 (P2), R11.2
unnamed: LED1.BAR_DISPLAY2 (P3), R12.2
unnamed: LED1.BAR_DISPLAY3 (P4), R13.2
unnamed: LED1.BAR_DISPLAY4 (P5), R14.2
unnamed: LED1.BAR_DISPLAY5 (P6), R15.2
unnamed: LED1.BAR_DISPLAY6 (P7), R16.2
unnamed: LED1.BAR_DISPLAY7 (P8), R17.2
unnamed: LED1.BAR_DISPLAY8 (P9), R18.2
unnamed: LED1.BAR_DISPLAY9 (P10), R19.2
PG: U3.26 (PC3(ADC3/PTCY)); also elsewhere on the board
RST: J10.5 (RESET), R9.1, U3.29 (PC6(RESET))
RXD: J12.1, U3.30 (PD0(PTCXY/OC3A/RXD0))
SCK: J10.7 (SCK), U3.17 (PB5(PTCXY/XCK1/SCK0))
SCL: J11.4; also elsewhere on the board
SDA: J11.2; also elsewhere on the board
TXD: J12.2, U3.31 (PD1(PTCXY/OC4A/TXD0))
VCC: C11.1, J9.2, R9.2, U3.4 (VCC), U3.18 (AVCC), U3.20 (AREF)


Board: 2 copper layers, 102.6 x 71.8 mm, 52 parts (0 on the bottom side), 53 nets.

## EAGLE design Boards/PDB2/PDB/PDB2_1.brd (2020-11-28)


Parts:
C1, C2, C3, C4: 2.2uF; 0603-CAP
C5: .1uF; 0603-CAP
CONN1, CONN2, CONN3: ANDERSONVERTICAL; ANDERSON_VERTICAL
D1: D_NRVB120VLSFT1G; ON_SEMI_SOD-123F
J1: XT60CONNECTOR
JP1: M041X04-MTA; 1X04-MTA
JP2, JP3, JP4, JP5: ATX
M1: CSD17577Q3A; DNH0008A; MANUFACTURER_PART_NUMBER CSD17577Q3A
R1, R2: 10k; R0603
R3, R4: 3.3k; R0603
R5, R6: 100k; R0603
R7: 5m; R2512
STANDOFF1, STANDOFF2, STANDOFF3, STANDOFF4, STANDOFF5, STANDOFF6: STAND-OFFTIGHT; STAND-OFF-TIGHT
SW1: PUSH_BUTTON; BUTTON_K12A
U1: BQ7692006PWRPW20-M; PW20-M

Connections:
3.3V: C4.2, R3.2, R4.2, U1.8 (REGOUT); also elsewhere on the board
5V: JP2.P$1, JP3.P$1, JP4.P$1, JP5.P$1; also elsewhere on the board
12V: CONN1.PIN1 (OUTB), CONN2.PIN2 (OUTA), CONN3.PIN2 (OUTA), D1.P (A), J1.12V, R1.2; also elsewhere on the board
ALERT: R5.1, U1.20 (ALERT); also elsewhere on the board
BCELL1: JP1.2, SW1.P$1, U1.16 (VC1)
BCELL2: JP1.3, U1.13 (VC4), U1.14 (VC3), U1.15 (VC2)
BCELL3: JP1.4, U1.12 (VC5)
BOOT: R2.2, SW1.P$2, U1.6 (TS1); also elsewhere on the board
CAP1: C3.2, U1.7 (CAP1)
DSG: M1.4 (GATE), R6.2, U1.1 (DSG)
GND: C1.1, C2.1, C3.1, C4.1, C5.2, J1.GND, JP1.1, R2.1, R5.2, R6.1, R7.2, U1.3 (VSS), U1.17 (VC0), U1.19 (SRN); also elsewhere on the board
GND_OUT: CONN1.PIN2 (OUTA), CONN2.PIN1 (OUTB), CONN3.PIN1 (OUTB), JP2.P$2, JP3.P$2, JP4.P$2, JP5.P$2, M1.5 (DRAIN_2), M1.6 (DRAIN_2), M1.7 (DRAIN_2), M1.8 (DRAIN_2), M1.9 (DRAIN_2); also elsewhere on the board
SCL: R3.1, U1.5 (SCL); also elsewhere on the board
SDA: R4.1, U1.4 (SDA); also elsewhere on the board
SRP: C5.1, M1.1 (SOURCE_2), M1.2 (SOURCE_2), M1.3 (SOURCE_2), R7.1, U1.18 (SRP)
VIN: C1.2, C2.2, D1.N (C), R1.1, U1.9 (REGSRC), U1.10 (BAT)


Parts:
C6, C7: 22uF; 0805
C8: .1uF; 0603-CAP
C9, C10, C11: 22uF; C0805
D2, D3: BZT52C2VXX_ZENER; SOD-123
L1: 3.3uH; MWSA0402S
R8, R10: 10k; R0603
R9: 56.2k; R0603
U2: TPS563200; SOT-23_6PIN_COPY

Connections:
5V: C9.1, C10.1, C11.1, D3.N, L1.P$1 (1), R9.2; also elsewhere on the board
12V: C6.2, C7.2, D2.N, R8.1, U2.P$3 (VIN); also elsewhere on the board
BST: C8.1, U2.P$6 (VBST)
FB: R9.1, R10.2, U2.P$4 (VFB)
GND_OUT: C6.1, C7.1, C9.2, C10.2, C11.2, D2.P, D3.P, R10.1, U2.P$1 (GND); also elsewhere on the board
unnamed: R8.2, U2.P$5 (EN)
SW: C8.2, L1.P$2 (2), U2.P$2 (SW)


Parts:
BUZ1: BUZZER3.3VBUZZER; BUZZER_3.3V
C12, C15, C16: 2.2uF; 0603-CAP
C13, C14: 18pF; 0603-CAP
J2: USB_B_PTH; USB-B-PTH
J3: AVR_SPI_PRG_6MA03-2; MA03-2
JP6: JMP-OPTION; 1X03-JMP-OPTION
LED1, LED2, LED3, LED4, LED5: LED0805; LED-0805
LED6: BAR_SEGMENT_DISPLAY
R11, R12: 22R; R0603
R13: 10k; R0603
R14, R15, R16, R17, R18: 330R; R0603
R19, R20, R21, R22, R23, R24, R25, R26, R27, R28: 220R; R0603
U3: ATMEGA32U4-AU; TQFP44
Y1: 8MHZ_X50328MSB2GI; SMD-5032_2P

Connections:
3.3V: JP6.1; also elsewhere on the board
ALERT: U3.21 ((TXD1/INT3)PD3); also elsewhere on the board
BOOT: U3.20 ((RXD1/INT2)PD2); also elsewhere on the board
BUZZ: BUZ1.P1 (A), U3.29 ((PCINT5/OC1A/OC4B/ADC12)PB5)
D+: J2.D+, R11.1
D-: J2.D-, R12.1
EN/MISO: J3.1, U3.11 ((PDO/PCINT3/MISO)PB3)
GND: BUZ1.P2 (C), C12.1, C13.1, C14.1, C15.1, C16.1, J2.GND, J2.SHLD1 (SHIELD), J2.SHLD2 (SHIELD), J3.6, LED1.C, LED2.C, LED3.C, LED4.C, LED5.C, LED6.BAR_DISPLAY10 (P11), LED6.BAR_DISPLAY11 (P12), LED6.BAR_DISPLAY12 (P13), LED6.BAR_DISPLAY13 (P14), LED6.BAR_DISPLAY14 (P15), LED6.BAR_DISPLAY15 (P16), LED6.BAR_DISPLAY16 (P17), LED6.BAR_DISPLAY17 (P18), LED6.BAR_DISPLAY18 (P19), LED6.BAR_DISPLAY19 (P20), U3.5 (UGND), U3.15 (GND), U3.23 (GND2), U3.33 ((HWB)PE2), U3.35 (GND3), U3.43 (GND4); also elsewhere on the board
LED1: R28.1, U3.39 ((ADC4/TCK)PF4)
LED2: R27.1, U3.40 ((ADC1)PF1)
LED3: R26.1, U3.41 ((ADC0)PF0)
LED4: R25.1, U3.1 ((INT6/AIN0)PE6)
LED5: R24.1, U3.27 ((T0/OC4D/ADC10)PD7)
LED6: R23.1, U3.26 ((T1/OC4D/ADC9)PD6)
LED7: R22.1, U3.32 ((ICP3/CLK0/OC4A)PC7)
LED8: R21.1, U3.31 ((OC3A/OC4A)PC6)
LED9: R20.1, U3.12 ((PCINT7/OC0A/OC1C/RTS)PB7)
LED10: R19.1, U3.30 ((PCINT6/OC1B/OC4B/ADC13)PB6)
MOSI: J3.4, U3.10 ((PDI/PCINT2/MOSI)PB2)
unnamed: C13.2, U3.17 (XTAL1), Y1.P$2 (2)
unnamed: R12.2, U3.3 (D-)
unnamed: R11.2, U3.4 (D+)
unnamed: C14.2, U3.16 (XTAL2), Y1.P$1 (1)
unnamed: C16.2, U3.6 (UCAP)
unnamed: LED6.BAR_DISPLAY0 (P1), R19.2
unnamed: LED6.BAR_DISPLAY1 (P2), R20.2
unnamed: LED6.BAR_DISPLAY2 (P3), R21.2
unnamed: LED6.BAR_DISPLAY3 (P4), R22.2
unnamed: LED6.BAR_DISPLAY4 (P5), R23.2
unnamed: LED6.BAR_DISPLAY5 (P6), R24.2
unnamed: LED6.BAR_DISPLAY6 (P7), R25.2
unnamed: LED6.BAR_DISPLAY7 (P8), R26.2
unnamed: LED6.BAR_DISPLAY8 (P9), R27.2
unnamed: LED6.BAR_DISPLAY9 (P10), R28.2
unnamed: R18.1, U3.8 ((SS/PCINT0)PB0)
unnamed: LED5.A, R18.2
unnamed: LED1.A, R14.2
unnamed: R14.1, U3.22 ((XCK1/CTS)PD5)
unnamed: R17.1, U3.36 ((ADC7/TDI)PF7)
unnamed: R16.1, U3.37 ((ADC6/TDO)PF6)
unnamed: R15.1, U3.38 ((ADC5/TMS)PF5)
unnamed: LED2.A, R17.2
unnamed: LED3.A, R16.2
unnamed: LED4.A, R15.2
PG: U3.28 ((PCINT4/ADC11)PB4)
RST: J3.5, R13.1, U3.13 (RESET)
SCL: U3.18 ((OSC0B/SCL/INT0)PD0); also elsewhere on the board
SCLK: J3.3, U3.9 ((PCINT1/SCLK)PB1)
SDA: U3.19 ((SDA/INT1)PD1); also elsewhere on the board
UVCC: C12.2, J2.VBUS, J3.2, JP6.3, U3.2 (UVCC), U3.7 (VBUS)
VCC: C15.2, JP6.2 (COMMON), R13.2, U3.14 (VCC), U3.24 (AVCC), U3.34 (VCC2), U3.42 (AREF), U3.44 (AVCC2)



Board: 2 copper layers, 112.1 x 89.7 mm, 81 parts (2 on the bottom side), 64 nets.

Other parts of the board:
U$1: PIE-LOGO-SMALL
U$2: OSHW-LOGO-L

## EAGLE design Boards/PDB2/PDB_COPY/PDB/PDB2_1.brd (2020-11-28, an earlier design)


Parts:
C1, C3, C17: 2.2uF; 0603-CAP
C2: 1uF; 0603-CAP
C4: .1uF; 0603-CAP
C11, C14: 10uF; .248"CAP_THRU
CONN1, CONN2, CONN3: ANDERSONVERTICAL; ANDERSON_VERTICAL
D2: D_MBR1020VL; SOD-123FL
J1: XT60CONNECTOR
JP1: M041X04-MTA; 1X04-MTA
JP2, JP3, JP4, JP5: ATX
M1: NMOS_CSD17579Q3A; DNH0008A; MANUFACTURER_PART_NUMBER CSD16401Q5
R1, R2: 10k; R0603
R3, R4: 3.3k; R0603
R5: 499k; R0603
R6: 100k; R0603
R7: 5m; SMD_SHUNT; MANUFACTURER_PART_NO WSHM28185L000FEA
STANDOFF1, STANDOFF2, STANDOFF3, STANDOFF4, STANDOFF5, STANDOFF7: STAND-OFFTIGHT; STAND-OFF-TIGHT
SW1: PUSH_BUTTON; BUTTON_K12A
U1: BQ7692006PWRPW20-M; PW20-M

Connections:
3.3V: C3.2, R3.2, R4.2, U1.8 (REGOUT); also elsewhere on the board
5V: C11.PLUS (+), C14.PLUS (+), JP2.P$1, JP3.P$1, JP4.P$1, JP5.P$1; also elsewhere on the board
12V: CONN1.PIN1 (OUTB), CONN2.PIN2 (OUTA), CONN3.PIN2 (OUTA), D2.P$2 (A), J1.12V, R1.2; also elsewhere on the board
ALERT: R5.1, U1.20 (ALERT); also elsewhere on the board
BCELL1: JP1.2, SW1.P$1, U1.16 (VC1)
BCELL2: JP1.3, U1.13 (VC4), U1.14 (VC3), U1.15 (VC2)
BCELL3: JP1.4, U1.12 (VC5)
BOOT: R2.2, SW1.P$2, U1.6 (TS1); also elsewhere on the board
CAP1: C2.2, U1.7 (CAP1)
DSG: M1.4 (GATE), R6.2, U1.1 (DSG)
GND: C1.1, C2.1, C3.1, C4.2, C17.1, J1.GND, JP1.1, R2.1, R5.2, R6.1, R7.P$1 (1), U1.3 (VSS), U1.17 (VC0), U1.19 (SRN); also elsewhere on the board
GND_OUT: C11.MINUS (-), C14.MINUS (-), CONN1.PIN2 (OUTA), CONN2.PIN1 (OUTB), CONN3.PIN1 (OUTB), JP2.P$2, JP3.P$2, JP4.P$2, JP5.P$2, M1.5 (DRAIN_2), M1.6 (DRAIN_2), M1.7 (DRAIN_2), M1.8 (DRAIN_2), M1.9 (DRAIN_2); also elsewhere on the board
SCL: R3.1, U1.5 (SCL); also elsewhere on the board
SDA: R4.1, U1.4 (SDA); also elsewhere on the board
SRP: C4.1, M1.1 (SOURCE_2), M1.2 (SOURCE_2), M1.3 (SOURCE_2), R7.P$2 (2), U1.18 (SRP)
VIN: C1.2, C17.2, D2.P$1 (C), R1.1, U1.9 (REGSRC), U1.10 (BAT)


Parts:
C5, C6: 10uF; 0805
C7: 8.2nF; 0603-CAP
C8: .1uF; 0603-CAP
C9, C18, C19: 22uF; C0805
L1: 3.3uH; MWSA0402S
R8, R11: 10k; R0603
R10: 56.2k; R0603
U2: Value; DDF0008A_N

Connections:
5V: C9.1, C18.1, C19.1, L1.P$1 (1), R10.2; also elsewhere on the board
12V: C5.2, C6.2, R8.1, U2.3 (VIN); also elsewhere on the board
BST: C8.1, U2.8 (VBST)
FB: R10.1, R11.2, U2.6 (VFB)
GND_OUT: C5.1, C6.1, C7.1, C9.2, C18.2, C19.2, R11.1, U2.1 (GND); also elsewhere on the board
unnamed: C7.2, U2.5 (SS)
unnamed: R8.2, U2.7 (EN)
SW: C8.2, L1.P$2 (2), U2.2 (SW)


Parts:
BUZ1: BUZZER3.3VBUZZER; BUZZER_3.3V
C10, C15, C16: 1uF; 0603-CAP
C12, C13: 18pF; 0603-CAP
J2: AVR_SPI_PRG_6MA03-2; MA03-2
J3: USB_B_PTH; USB-B-PTH
JP7: JMP-OPTION; 1X03-JMP-OPTION
LED1, LED2, LED3, LED4, LED5: LED0805; LED-0805
LED6: BAR_SEGMENT_DISPLAY
R12: 10k; R0603
R13, R14, R15, R16, R17: 220R; R0603
R18, R19, R20, R21, R22, R23, R24, R25, R26, R27: 150R; R0603
R28, R29: 22R; R0603
U3: ATMEGA32U4-AU; TQFP44
Y1: CRYSTAL10.5X4.8; CRYSTAL-SMD-10.5X4.8-2PIN; PART_NO ECS-160-20-3X-EN-TR

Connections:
3.3V: JP7.1; also elsewhere on the board
ALERT: U3.21 ((TXD1/INT3)PD3); also elsewhere on the board
BOOT: U3.20 ((RXD1/INT2)PD2); also elsewhere on the board
BUZZ: BUZ1.P1 (A), U3.29 ((PCINT5/OC1A/OC4B/ADC12)PB5)
D+: J3.D+, R29.1
D-: J3.D-, R28.1
EN/MISO: J2.1, U3.11 ((PDO/PCINT3/MISO)PB3)
GND: BUZ1.P2 (C), C10.1, C12.1, C13.1, C15.1, C16.1, J2.6, J3.GND, J3.SHLD1 (SHIELD), J3.SHLD2 (SHIELD), LED1.C, LED2.C, LED3.C, LED4.C, LED5.C, LED6.BAR_DISPLAY10 (P11), LED6.BAR_DISPLAY11 (P12), LED6.BAR_DISPLAY12 (P13), LED6.BAR_DISPLAY13 (P14), LED6.BAR_DISPLAY14 (P15), LED6.BAR_DISPLAY15 (P16), LED6.BAR_DISPLAY16 (P17), LED6.BAR_DISPLAY17 (P18), LED6.BAR_DISPLAY18 (P19), LED6.BAR_DISPLAY19 (P20), U3.5 (UGND), U3.15 (GND), U3.23 (GND2), U3.33 ((HWB)PE2), U3.35 (GND3), U3.43 (GND4); also elsewhere on the board
LED1: R27.1, U3.39 ((ADC4/TCK)PF4)
LED2: R26.1, U3.40 ((ADC1)PF1)
LED3: R25.1, U3.41 ((ADC0)PF0)
LED4: R24.1, U3.1 ((INT6/AIN0)PE6)
LED5: R23.1, U3.27 ((T0/OC4D/ADC10)PD7)
LED6: R22.1, U3.26 ((T1/OC4D/ADC9)PD6)
LED7: R21.1, U3.32 ((ICP3/CLK0/OC4A)PC7)
LED8: R20.1, U3.31 ((OC3A/OC4A)PC6)
LED9: R19.1, U3.12 ((PCINT7/OC0A/OC1C/RTS)PB7)
LED10: R18.1, U3.30 ((PCINT6/OC1B/OC4B/ADC13)PB6)
MOSI: J2.4, U3.10 ((PDI/PCINT2/MOSI)PB2)
unnamed: C12.2, U3.17 (XTAL1), Y1.P$2 (2)
unnamed: R28.2, U3.3 (D-)
unnamed: R29.2, U3.4 (D+)
unnamed: C13.2, U3.16 (XTAL2), Y1.P$1 (1)
unnamed: C16.2, U3.6 (UCAP)
unnamed: LED6.BAR_DISPLAY0 (P1), R18.2
unnamed: LED6.BAR_DISPLAY1 (P2), R19.2
unnamed: LED6.BAR_DISPLAY2 (P3), R20.2
unnamed: LED6.BAR_DISPLAY3 (P4), R21.2
unnamed: LED6.BAR_DISPLAY4 (P5), R22.2
unnamed: LED6.BAR_DISPLAY5 (P6), R23.2
unnamed: LED6.BAR_DISPLAY6 (P7), R24.2
unnamed: LED6.BAR_DISPLAY7 (P8), R25.2
unnamed: LED6.BAR_DISPLAY8 (P9), R26.2
unnamed: LED6.BAR_DISPLAY9 (P10), R27.2
unnamed: R17.1, U3.8 ((SS/PCINT0)PB0)
unnamed: LED5.A, R17.2
unnamed: LED1.A, R13.2
unnamed: R13.1, U3.22 ((XCK1/CTS)PD5)
unnamed: R16.1, U3.36 ((ADC7/TDI)PF7)
unnamed: R15.1, U3.37 ((ADC6/TDO)PF6)
unnamed: R14.1, U3.38 ((ADC5/TMS)PF5)
unnamed: LED2.A, R16.2
unnamed: LED3.A, R15.2
unnamed: LED4.A, R14.2
PG: U3.28 ((PCINT4/ADC11)PB4)
RST: J2.5, R12.1, U3.13 (RESET)
SCL: U3.18 ((OSC0B/SCL/INT0)PD0); also elsewhere on the board
SCLK: J2.3, U3.9 ((PCINT1/SCLK)PB1)
SDA: U3.19 ((SDA/INT1)PD1); also elsewhere on the board
UVCC: C10.2, J2.2, J3.VBUS, JP7.3, U3.2 (UVCC), U3.7 (VBUS)
VCC: C15.2, JP7.2 (COMMON), R12.2, U3.14 (VCC), U3.24 (AVCC), U3.34 (VCC2), U3.42 (AREF), U3.44 (AVCC2)



Board: 2 copper layers, 112.1 x 89.7 mm, 82 parts (2 on the bottom side), 65 nets.

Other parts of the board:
U$1: PIE-LOGO-SMALL
U$2: OSHW-LOGO-L

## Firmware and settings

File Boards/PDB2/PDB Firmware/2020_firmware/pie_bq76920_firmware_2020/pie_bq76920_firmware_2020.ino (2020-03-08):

#include <pie_bq76920_lib.h>

#define MIN_cells_LEVEL  3400
#define MAX_CURRENT_LEVEL   20000
  
#define BAR_LED1  A3
#define BAR_LED2  A4
#define BAR_LED3  A5
#define BAR_LED4  7
#define BAR_LED5  6
#define BAR_LED6  12
#define BAR_LED7  13
#define BAR_LED8  5
#define BAR_LED9  11
#define BAR_LED10 10

#define BUZZER    9
#define BOOT      0
#define ALERT     1
#define UV_LED    A2
#define _12V_FG_LED  A1


pie_bq76920_lib bmic;
int16_t cells[5];
uint8_t buzzer_on = 0;

int32_t current = 0;

int bar_led_array[] = {BAR_LED1, BAR_LED2, BAR_LED3, BAR_LED4, BAR_LED5, BAR_LED6, BAR_LED7, BAR_LED8, BAR_LED9, BAR_LED10};

void print_status(uint8_t status) {
  Serial.print("status: "); Serial.println(status);
  if (bmic.check_status(status, DEVICE_XREADY_FAULT)) Serial.println("DEVICE XREADY FAULT");
  if (bmic.check_status(status, OVRD_ALERT_FAULT)) Serial.println("OVRD ALERT FAULT");
  if (bmic.check_status(status, UV_FAULT)) Serial.println("UV_FAULT");
  if (bmic.check_status(status, OV_FAULT)) Serial.println("OV FAULT");
  if (bmic.check_status(status, SCD_FAULT)) Serial.println("SCD FAULT");
  if (bmic.check_status(status, OCD_FAULT)) Serial.println("OCD FAULT");
  if (bmic.check_status(status, CC_READY_FAULT)) Serial.println("CC READY FAULT");
}

void display_battery_level() {
  int16_t min_cells_voltage = cells[0];
  if (cells[1] < min_cells_voltage) min_cells_voltage = cells[1];
  if (cells[4] < min_cells_voltage) min_cells_voltage = cells[4];

  int16_t normalized_level = (min_cells_voltage - MIN_cells_LEVEL) * .0125;
  Serial.print("Normalzed Battery Level: "); Serial.println(normalized_level);
  if (normalized_level < 10) normalized_level++;

  for (int i = 0; i < normalized_level; i++) digitalWrite(bar_led_array[i], HIGH);
  for (int i = normalized_level; i < 10; i++) digitalWrite(bar_led_array[i], LOW);
}

void setup() {
  // put your setup code here, to run once:
  Serial.begin(115200);
  pinMode(BAR_LED1, OUTPUT);
  pinMode(BAR_LED2, OUTPUT);
  pinMode(BAR_LED3, OUTPUT);
  pinMode(BAR_LED4, OUTPUT);
  pinMode(BAR_LED5, OUTPUT);
  pinMode(BAR_LED6, OUTPUT);
  pinMode(BAR_LED7, OUTPUT);
  pinMode(BAR_LED8, OUTPUT);
  pinMode(BAR_LED9, OUTPUT);
  pinMode(BAR_LED10, OUTPUT);

  pinMode(BUZZER, OUTPUT);
  pinMode(BOOT, INPUT);
  pinMode(ALERT, INPUT);
  pinMode(UV_LED, OUTPUT);
  pinMode(_12V_FG_LED, OUTPUT);
  delay(900);
  
  bmic.init();
  bmic.enable_cc();
  bmic.write_SCD(SCD_70_US_DELAY, SCD_67_MV_THRESHOLD);
  bmic.write_OCD(OCD_8_MS_DELAY, OCD_50_MV_THRESHOLD);
  bmic.write_UV_trip(MIN_cells_LEVEL);
  bmic.write_OV_trip(4300);
  bmic.write_UV_and_OV_delay(UV_8_SEC_DELAY, OV_2_SEC_DELAY);
  
  bmic.write_rsns(true);
  bmic.dsg_on();
}

void loop() {
  if (digitalRead(BOOT)) bmic.shutdown();
  uint8_t status;
  status = bmic.get_status();
  print_status(status);
  
  bmic.read_battery_cells(cells);
  for(int i = 0; i < 5; i++) {
    Serial.print("cells "); Serial.print(i); Serial.print(": "); Serial.println(cells[i]);
  }
  if (cells[0] <= MIN_cells_LEVEL || cells[1] <= MIN_cells_LEVEL || cells[4] <= MIN_cells_LEVEL) {
    for (int i = 0; i < 10; i++) {
      digitalWrite(bar_led_array[i], LOW);
    }
    digitalWrite(UV_LED, HIGH);
    analogWrite(BUZZER, 200);

    for (int i = 0; i < 50; i++) {
      Serial.println("UNDERVOLTAGE DETECTION!!!");
      delay(100);
    }
    bmic.shutdown();
  }
  
  display_battery_level();
  
  current = bmic.read_current() / 5;
  if (current >= MAX_CURRENT_LEVEL) {
    bmic.dsg_off();
    for (int i = 0; i < 10; i++) {
    digitalWrite(bar_led_array[i], LOW);
  }
  digitalWrite(_12V_FG_LED, HIGH);

  for (int i = 0; i < 100; i++) {
    Serial.println("OVERCURRENT/SHORTCIRCUIT DETECTION!!!");
    delay(100);
  }
  bmic.shutdown();
  }

  Serial.print("Current: "); Serial.println(current);
  Serial.print("ALERT: "); Serial.println(digitalRead(ALERT));  
  Serial.print("BOOT: "); Serial.println(digitalRead(BOOT));
  
  Serial.println();
  delay(250);
}

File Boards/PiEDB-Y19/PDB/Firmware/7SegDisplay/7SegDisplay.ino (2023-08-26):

//Created by aboda243
//Modified by Justin H. for Pioneers in Engineering
//Used in Pioneer in Engineering's battery display on PDB
//https://create.arduino.cc/projecthub/aboda243/how-to-use-4-digit-7-segment-without-library-b8e014

#include <Wire.h>

#define expander B0100000 

#define D1 A0
#define D2 15
#define D3 14
#define D4 9
#define BUZZER 10
#define Cell1 A3
#define Cell2 A2
#define Cell3 A1
#include "array.h"
#include "functions.h"

//test push
void setup() {                

  pinMode(D1, OUTPUT);  
  pinMode(D2, OUTPUT);  
  pinMode(D3, OUTPUT);  
  pinMode(D4, OUTPUT); 
  Serial.begin(9600);
  pinMode(A3, INPUT);
  pinMode(A2, INPUT);
  pinMode(A1, INPUT);
  pinMode(BUZZER, OUTPUT);
  Wire.begin();
}
//long previousTime = 0;
// the loop routine runs over and over again forever:
void loop() {
  //unsigned long currentTime = millis();
  analogReference(DEFAULT);
  //float* voltages = parseVoltage(analogRead(Cell1), analogRead(Cell2), analogRead(Cell3));
  float r_v1 = (float) analogRead(Cell1);
  float v_v1 = r_v1 * 20.0/1023.0;
  String o_v1 = DisplayChars(String(v_v1));
  
  float r_v2 = (float) analogRead(Cell2);
  float v_v2 = (r_v2 * 20.0/1023.0) - v_v1;
  String o_v2 = DisplayChars(String(v_v2));
  
  float r_v3 = (float) analogRead(Cell3);
  float v_v3 = (r_v3 * 20.0/1023.0) - v_v2 - v_v1;
  String o_v3 = DisplayChars(String(v_v3));
  
  float r_all = (float) analogRead(Cell3);
  float v_all = r_v3 * 20.0/1023.0;
  String o_all = DisplayChars(String(v_all));

  //tone(10, 1000);
  //else if (v_all > 12 && v_v1 > 4.0 && v_v2 > 4.0 && v_v3 > 4.0) {
    //noTone(BUZZER);
  //}
  //Serial.println(o_v1);
  Serial.println("ur mom... lol -Justin");

  displayString("CEL1", 2000);
  displayString(o_v1, 2000);
  displayString("CEL2", 2000);
  displayString(o_v2, 2000);
  displayString("CEL3", 2000);
  displayString(o_v3, 2000);
  displayString("ALL ", 2000);
  displayString(o_all, 2000);

}

void displayString(String phrase, int length) {
  for (int i = 0; i < length/8; i++) {
    printDigit(phrase[0], D1);
    delay(2);
    printDigit(phrase[1], D2);
    delay(2);
    printDigit(phrase[2], D3);
    delay(2);

    printDigit(phrase[3], D4);

    
    delay(2);
  }
}

/* Voltage divider divides voltages by 4.
   outputs voltage of the 3 cells in a float array. */
float* parseVoltage(int pin1, int pin2, int pin3) {
  float voltage1 = (float) pin1 * 20 / 1023;
  float voltage2 = (float) pin2 * 20 / 1023;
  float voltage3 = (float) pin3 * 20 / 1023;
  float output[] = {0.0, 0.0, 0.0};
  output[0] = voltage1;
  output[1] = voltage2 - voltage1;
  output[2] = voltage3 - voltage2;
  //Serial.println(voltage1);
  return output;
}
//for(int ti = 0 ; ti <= (Delay / delay_factor) ; ti++) { //continously flashes characters for DELAY duration
  //printDigit(toPrint[0], D1);
  //delay(2);
  //printDigit(toPrint[1], D2);
  //delay(2);
  //printDigit(toPrint[2], D3);
  //delay(2);
  //printDigit(toPrint[3], D4);
  //delay(2);
  //}

void expanderWrite(byte _data) {
  Wire.beginTransmission(expander);
  Wire.write(_data);
  Wire.endTransmission(); 
}

void reset() { 
  digitalWrite(D1, LOW);
  digitalWrite(D2, LOW);
  digitalWrite(D3, LOW);
  digitalWrite(D4, LOW);
  expanderWrite(0b11111111);
  //for(byte i = 0 ; i < 8 ; i++){
    //digitalWrite(seg[i], HIGH); //mode = 1; for each segment, 1 = off and 0 = on
  //}
}

int printDigit(char Chara, int digitPort) { 
  reset(); 
  int character = -1;
  digitalWrite(digitPort, HIGH);
  for(int i = 0 ; i < charsInArray ; i++) {
    if (Chara == Char[i][1]) { //set character equal to the corresponding array index
     character = i;
    }
  }
  expanderWrite(~Char[character][0]);
  
}

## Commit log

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2016-09-20 Update PiE lbr
    Follow
    https://github.com/pioneers/tenshi/pull/320#issuecomment-248368896
    for more info.
    TL;DR: Update the screw terminals to be more descriptive and reflect
    their actual reallife look
2016-09-20 initial commit of battery buzzer brd and sch files
    copy-pastaed from the tenshi repo.
    [battery_buzzer.brd, battery_buzzer.sch]
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2016-09-21 Move around pie logo
    [ServoController.brd]
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2016-09-23 Change rev for servo
    [ServoController.sch]
2016-09-23 Added 7 segment array & calibration.
    also nuked board file, it'd have to change too much anyway.
    Have just enough I/O for the calibration button + calibration button
    [battery_buzzer.brd, battery_buzzer.sch]
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2016-09-23 added DPST switch to libary, added power bypass to buzzer
    power bypass so that with the push of a button the buzzer can turn out
    powered by the battery alone.
    [battery_buzzer.brd, battery_buzzer.sch]
2016-09-23 final additions to the battery buzzer schematic
    cleaned things up, added the obligatory debug features.
    [battery_buzzer.brd, battery_buzzer.sch]
2016-09-23 some more pinremapping
    to make routing easier... but routing starting now.
    [battery_buzzer.brd, battery_buzzer.sch]
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2016-09-23 switched some pin assignments
    to make routing easier.
    [battery_buzzer.brd, battery_buzzer.sch]
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2016-09-23 and yet more pin remapping.
    [battery_buzzer.brd, battery_buzzer.sch]
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2016-09-23 silkscreen done
    0 DRC errors.
    [battery_buzzer.brd, battery_buzzer.sch]
2016-09-23 added the neccessary disclamers & logos.
    [battery_buzzer.brd]
2016-09-23 arduino code for breadboard battery buzzer.
    [battery_buzzer_test.ino]
2016-09-23 fixed proportional font issues.
    updated library, too.
    [battery_buzzer.brd]
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2016-09-23 Initialize Screw Terminal Rev A
    [SCREW.brd, SCREW.sch]
2016-09-23 Initialize Screw Terminal with Arduino ProMicro
    [SCREW.sch]
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2016-09-24 Initial commit for Yogi Bear Motor Controller - Added Stanley Liu's schematic - Started initial board layout
    [YogiBear.brd, YogiBear.sch]
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2016-09-24 Add team flag EAGLE files to SmartSensor repo
    [team_flag.brd, team_flag.sch]
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2016-09-24 REVIEW CHECK: Fix name on APM
    [team_flag.brd, team_flag.sch]
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2016-09-26 Replaced reverse polarity diode with PiE library generic diode package
    [YogiBear.brd, YogiBear.sch]
2016-09-26 Updated Pro Micro package to new library part - updated silkscreen
    [ServoController.brd, ServoController.sch]
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2016-09-30 Minor fixes everywhere
    [LoadCell.brd, LoadCell.sch, Screw.brd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]
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2016-10-01 Extra additions on vector font?
    Probably just hte xml values for transparency changing.
    [battery_buzzer.brd, battery_buzzer.sch]
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2016-10-08 Finish and flip RFID board
    [RFIDELMH.brd]
2016-10-08 Arrange TwistIt to be smaller with all components under arduino
    [Screw.brd]
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2016-10-13 Correcting board pin comments
    [ServoController.brd]
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2016-10-14 arduino code demonstrates all functionality (basic) for battery buzzer.
    [battery_buzzer_test.ino]
2016-10-20 Add files via upload
    Mounting Holes Issue #5
    [Screw.brd]
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2016-10-21 Add screw terminals and names; change orientation to be ergonomic
    [Screw.brd, Screw.sch]
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2016-10-22 Rerouting for 45 degrees, prop. to vector font
    [RFID.brd]
2016-10-22 Arduino test code for Buzzer rev 9A
    [battery_buzzer_test.ino]
2016-10-22 Editing for silkscreen conflicts, resizing fonts and whatnot
    [LoadCell.brd, Screw.brd, battery_buzzer.brd]
2016-10-22 Fix Battery Buzzer 9A erratta
    Updated 7-segment and DPST parts.
    Connected unconnected wire. Re-ordered a few pins on the arduino to
    make wiring cleaner.
    [battery_buzzer.brd, battery_buzzer.sch]
2016-10-25 Updated Revision Number on battery buzzer.
    Changed to Rev 9B, (forgot to do that last time).
    [battery_buzzer.brd, battery_buzzer.sch]
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2016-10-30 Add battery buzzer to board
    [PDB_MH.brd, PDB_MH.sch]
2016-10-30 Reroute battery buzzer into PDB #1
    [PDB_MH.brd]
2016-10-30 Fix LED and Motor Controller
2016-10-30 Fix spacing for RFID
    [RFID.brd, RFID.sch]
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2016-10-30 Complete integration of BatteryBuzzer in PDB. Change connector orientation from issues.
    [PDB_MH.brd]
2016-10-30 Move screwterminal labels, adjust schematic spacing for clarity
    [Screw.brd, Screw.sch]
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2016-10-31 Correct trace width and create less complex routing.
    [PDB_MH.brd]
2016-10-31 Change width of 5V rail; move U mounting hole
    [PDB.brd]
2016-10-31 TI chip added into schematic.
    Major Schematic changes. Board not yet routed.
    [battery_buzzer.brd, battery_buzzer.sch]
2016-10-31 Updates
    Did the current sense resistor calcs, changed part to match. (God is
    that a huge resistor).
    Did initial layout of board, no routes. Will look at tomorrow.
    [battery_buzzer.brd, battery_buzzer.sch]
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2016-11-01 Added i2c Pulldowns, more organizing
    now ready to put down wires.
    [battery_buzzer.brd, battery_buzzer.sch]
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2016-11-01 Update library parts and fix the text
    [PDB.brd, PDB.sch]
2016-11-01 Fix silk screen conflicts and add cam job
    [PDB.brd]
2016-11-01 Add Battery Buzzer gerb
2016-11-01 Fix board outline alignment
    [battery_buzzer.brd]
2016-11-01 Add fixed revb gerber
2016-11-02 Fix small things for Servo and Twistit
    [ServoController.brd, TwistIt.brd, TwistIt.sch]
2016-11-03 Add encoder, start adding bom info to library
    [TwistIt.brd, TwistIt.sch]
2016-11-05 Add more info to lbr; remove 5V from motor controlle rbreakout on twistit
    [TwistIt.brd, TwistIt.sch]
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2016-11-10 Fix the arduino smd footprint
2016-11-10 Replace the apm with surface mount; needs routing
    [TeamFlag.brd, TeamFlag.sch]
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2016-11-11 Silk screen fixes
    [TeamFlag.brd]
2016-11-11 Fix silkscreen alignment on apmsmd
2016-11-12 Rebase PDB schematic version that includes battery buzzer
    [PDB.sch]
2016-11-12 Fix rst pin
2016-11-13 Fix pins, change test
    [RFID.brd, RFID.sch]
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2016-11-18 Fixed backwards-annotation error caused by blatntly wrong .sch file.
    Did so by checking out the right commit (as verified by Mohammed), and copy-pastaing.
    [PDB.sch]
2016-11-18 Moved battery buzzer test code to PDB, renamed.
    [SevenSeg.cpp, test_code.ino]
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2016-11-18 Fix the drill sizes on rfid
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2016-11-18 Update the MOSFET part to use pie lbrs thing
    [TeamFlag.brd, TeamFlag.sch]
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2016-11-20 Rearange encoder to account for pullout and update parts
    [TwistIt.brd, TwistIt.sch]
2016-11-20 Fix keepout issue for led 0805
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2016-11-21 Fix CIRC_BREAKER pckg offset; change name/val size for DPDT_SW and MOSFETs; update all parts to SS/pie.lbr
    [PDB.brd, PDB.sch]
2016-11-21 Add back resistor values for battery buzzer
    [PDB.brd, PDB.sch]
2016-11-22 Change Buck Converter mounting hole size and tKeepout, ATX connectors, remove SJ1, add Fuses
    [PDB.brd, PDB.sch]
2016-11-22 Fix some mirrored components
    [RFID.brd]
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2016-11-22 Add resistors 5V Rail; Correct silkscreen
    [PDB.brd, PDB.sch]
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2016-11-22 Fix vector fonts and add frame
    [RFID.brd, RFID.sch]
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2016-11-22 Impliment multiple display features & wiping EEPROM
    Now wipe EEPROM if there already is a calibration when button is
    pressed.
    Will then calibrate correctly on next button press.
    Now show "Calibration" "Done" + calibration value on calibration.
    Now show "Calibration" "Clear" on EEPROM wipe (when done via button).
    [disp_8.ino, voltage_sense.ino]
2016-11-22 Dimension fixes; tkeepout changes
    [TeamFlag.brd, TeamFlag.sch]
2016-11-22 Fix fonts
    [TwistIt.brd, TwistIt.sch]
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2016-11-22 Change silkscreen; Add COTS battery buzzer and values to resistors; Redo vias and R17
    [PDB.brd, PDB.sch]
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2016-11-23 add new DRC for 2oz copper with BAC
    added 2 thou to tolerances to "play it safe" -- we've been noticing
    board shorts.
2016-11-23 Various Fixes to bring PDB to 2oz copper standards
    Specifically,
    - Fixed serval issues that resulted from 2oz copper DRC.
    - Fixed minor silkscreen issues.
    - Fixed many of the groundplanes not moving at right angles
    - Fixed location of R16 (calib jumper resistor), moving it next to the
    calibration header. That really cleaned up routing.
    - Moved calibration jumper to edge of board.
    [PDB.brd, PDB.sch]
2016-11-23 Fix all fonts
    [PDB.brd]
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2016-12-08 Fix ATX and ARM SM
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2016-12-08 Change Calibrate Button Functionality
    To calibrate after-press, not during-press.
    PCB issue makes this a neccessity for accurate measurements. Don't know
    why, though.
    [voltage_sense.ino]
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2017-01-03 Update the ATX part and move around to fit board
    [PDB.brd, PDB.sch]
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2017-01-17 Fix scaling on laser stencil
2017-02-01 Fix drill hole sizes for 2,3,4 pin screw headers.
    If you're using these parts on your board, you'll need to update the library "Library -> Update All" to use this new part
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2017-02-04 fixed formatting errors for Averal.
    [gui.py]
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2017-02-04 Finished product (disco still doesnt' work though. Or buzzers)
    [gui.py]
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2017-02-18 Made it so it won't crash when you load images.
    [gui.py]
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2017-05-31 Fix servo readme
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2017-06-02 Replaced SPDT with SP3T slide switch, and fixed teamflag v2
    [TeamFlag.brd, TeamFlag.sch]
2017-06-02 Fixed some issues with SP3T switch and board layout
    [TeamFlag.brd, TeamFlag.sch]
2017-06-07 Fixed clearence issues with the SP3T slide
    [TeamFlag.brd, TeamFlag.sch]
2017-06-07 Fixed board with new part updates
    [TeamFlag.brd, TeamFlag.sch]
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2017-07-02 Deleted old team flag from main folder. It still exists in Y9 folder
    [TeamFlag.brd, TeamFlag.sch]
2017-07-08 Fix the routing issues
    [TeamFlag.brd]
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2017-08-19 team flag fixed <3 margo
    [TeamFlag.brd, TeamFlag.sch]
2017-08-19 fixed a thing in team flag
    [ServoController.sch]
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2017-09-07 Fixed a 90 deg angle
    [test_board.brd]
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2017-09-21 Labeled Servos correctly and changed rev cycle
    [ServoController.brd, ServoController.sch]
2017-09-21 Updated Rev on frames (does not necessarily mean that everything is good-to-go)
    [LoadCell.sch, PDB.sch, RFID.sch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]
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2017-10-07 made hole guys smaller for usb and labeled positive one
    [TeamFlag.brd]
2017-10-14 margo moved the arduino slightly to the left so it doesn't touch the hole guy
    [RFID.brd]
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2017-10-14 margo altered resistor alignment to please seiya's ocd
    [TwistIt.brd]
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2017-10-14 fixed the actual thing seiya wanted -- moved the arduino(?) to the middle between the pillar/hole things
    [RFID.brd]
2017-10-14 actually actually fixed the thing seiya wanted -- the arduino is centered and the rfid is correctly moved -- also hopefully the drill hole matches up with the other thing (top right corner)
    [RFID.brd]
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2017-10-28 Added back 5V buck and added caps. DRC clean
    [PDB.brd, PDB.sch]
2017-11-02 Please, PDB, please work. Also I updated ATX connector.
    [PDB.brd, PDB.sch]
2017-11-09 vital important work changing rev to prod i am a very significant part of this team -- team flag
    [TeamFlag.brd, TeamFlag.sch]
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2018-07-07 Created new 5PIN part to replace screw terminal
    [TwistIt.sch]
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2018-07-08 Created rough version of sensor board, split from TwistIt
    [SensorBoard.brd, SensorBoard.sch]
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2018-07-10 Revised SensorBoard and fixed TwistIt
    [SensorBoard.brd, SensorBoard.sch, TwistIt.brd]
2018-07-15 Split motor controller from TwistIt and modified resistor array to account for size errors
    [MotorController.brd, MotorController.sch]
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2018-07-26 Completed rough version of motor controller chip board
    [MotorControllerChipTest.brd, MotorControllerChipTest.sch]
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2018-07-26 Fixed font style for some text
    [MCChipProto.brd]
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2018-09-06 Fixed some issues
    [MotorController.brd, SensorBoard.sch]
2018-09-06 Fixed LED color values not showing up
    [MotorController.brd]
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2018-10-27 Fixed routing to arduino pins
    [MotorController.brd, MotorController.sch]
2018-10-27 Fixing sizes
    [MotorController.brd, MotorController.sch]
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2019-07-25 connected remaining pins on 32U4, added USB B and USB Micro
    [MCDB.sch]
2019-07-25 added many capacitors (to USB D lines, to digital logic VCC for each MC, and three to VPWR)
    [MCDB.sch]
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2019-08-15 goddamn u sherwin; also deleted one unnecessary polygon
    [MCDB.brd]
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2019-08-23 finished PDB, motorcontroller test board, and updates to pie lib
    [2019-07-28_21-42-17.sch, MDBU010A(001)_BOM.xls, PDB Rev2 Digikey Cart.csv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]
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2019-11-17 fixed silkscreen fonts and ground pins
    [breakout.brd, breakout.sch]
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2019-12-05 fixed lib
    [PDB2_1.brd, PDB2_1.sch]
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2019-12-27 fixed pdb drc
    [PDB2_1.brd, PDB2_1.sch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]
2019-12-27 Fixed drc errors, generated new gerb
    [PDB2_1.brd]
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2020-08-29 did the pcb stuff for the distancce sensor
    [breakout.brd, breakout.sch]
2020-09-03 it all works now finally, (ultrasonic ir boards)
    [breakout.brd, breakout.sch]
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2021-02-13 maybe fixed
    [linefollower.brd]
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2024-04-26 Put TTL Converter in correct folder
    [BOM.csv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]
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2024-09-21 updated TurboPCB schematic and footprint; incomplete connector socket footprint assignment
    [Turbo PCB Design.kicad_pcb, Turbo PCB Design.kicad_sch]
2024-10-12 added 1mm through-hole pad to PiE footprint library for onboarding. Finished onboarding footprint.
    [Turbo PCB Design.kicad_pcb, Turbo PCB Design.kicad_sch]
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2026-01-15 added 2024-2025 buck converter test board and updated libraries to include custom footprint and symbol for LM25085-Q1 buck switching controller
    [bom.csv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]

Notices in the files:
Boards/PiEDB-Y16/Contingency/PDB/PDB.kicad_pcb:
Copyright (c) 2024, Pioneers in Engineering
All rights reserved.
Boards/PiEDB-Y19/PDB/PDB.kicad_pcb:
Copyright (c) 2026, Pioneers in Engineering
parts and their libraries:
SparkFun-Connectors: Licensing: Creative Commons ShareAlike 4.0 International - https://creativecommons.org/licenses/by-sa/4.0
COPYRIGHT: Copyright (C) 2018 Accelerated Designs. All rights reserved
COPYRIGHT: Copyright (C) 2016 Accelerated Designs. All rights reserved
